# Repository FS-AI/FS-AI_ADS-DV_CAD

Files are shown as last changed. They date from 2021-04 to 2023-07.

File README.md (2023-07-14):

# FS-AI_ADS-DV_CAD

## Introduction

This repository contains CAD data for the IMechE FS-AI ADS-DV for release to participating teams.

The CAD provided is a subset of the whole vehicle CAD and is intended for sensor and / or compute hardware installation and vehicle dynamics modelling purposes.

In particular teams wishing to fit additional sensors and / or compute hardware to a shared IMechE ADS-DV must use this CAD data to gain approval for their installation design. (See section 'Additional Sensor and Compute Mounting CAD Submission and Approval' below).

This CAD data remains Copyright IMechE 2020 and must not be uploaded to alternate public access web / cloud locations. This is both to protect copyright and to ensure there is one 'official' source for CAD data that may be up-issued by the IMechE as necessary. Local clones are encouraged to make it easy for updates to be pulled from the upstream repository using Git.

The URL for this repository is: https://github.com/FS-AI/FS-AI_ADS-DV_CAD

If you are not accessing this repository directly from this URL then likely you are working from a fork or clone which may not contain the latest data or information. If you have made a local clone, please ensure you do a 'git pull' to ensure you have the latest version of all files.

## Updates

The repository will be updated regularly in response to questions and as new information is confirmed and released. Github allows you to 'Watch' the repository so as to be informed of activity.

#### Update 2023-02-23

Clarified that both additional sensor and compute installations are allowed.

#### Update 2021-06-02

CAD models of the various connector types have been added.

## Questions

Please use the Github 'Issues' feature to ask questions regarding this repository. Please label your issue with the tag 'question'.

Best efforts will be made to answer all questions but please allow a few days for a response.

If a general forum style chat is more appropriate, please use the Github 'Discussions' feature.

## Content

The repository consists of the following files:

- 'Readme.md' - this file containing information about the repository.
- '\images' - folder containing the images for 'Readme.md'.
- 'FS-AI_ADS-DV_CAD.f3d' - see below.
- 'FS-AI_ADS-DV_CAD.step' - see below.
- '12V_Power_Mated' .f3d & .step' (added 2021-06-02)
- 'CAN_DE9_Mated'  .f3d & .step' (added 2021-06-02)
- 'RJ45_Ethernet'  .f3d & .step' (added 2021-06-02)
- 'USB_Mated'  .f3d & .step' (added 2021-06-02)

### Fusion 360 File 'FS-AI_ADS-DV_CAD.f3d'

This file is provided in native Fusion 360 format, which means it preserves sketch details, section analysis details and other useful data such as construction geometry.

Fusion 360 is available free-of-charge for non-commercial or educational use. Full details at: https://www.autodesk.co.uk/products/fusion-360/personal

See also this video for information on how to correctly activate the Personal edition of Fusion 360 instead of the 30 day free trial: https://www.youtube.com/watch?v=qJABXBvuoB4&ab_channel=DesktopMakes

### STEP File 'FS-AI_ADS-DV_CAD.step'

This file is a STEP format export of the Fusion 360 file. STEP is a universal file format for import into other CAD packages.

One disadvantage of the STEP format is that it does not preserve the sketch details of the Front and Side view relating to the Surface Envelope definition and the ZED camera sight line. You will need to replicate this sketch geometry within your own CAD package. See the images below.

This STEP file has been tested with FreeCAD v0.19, available here: https://www.freecadweb.org/

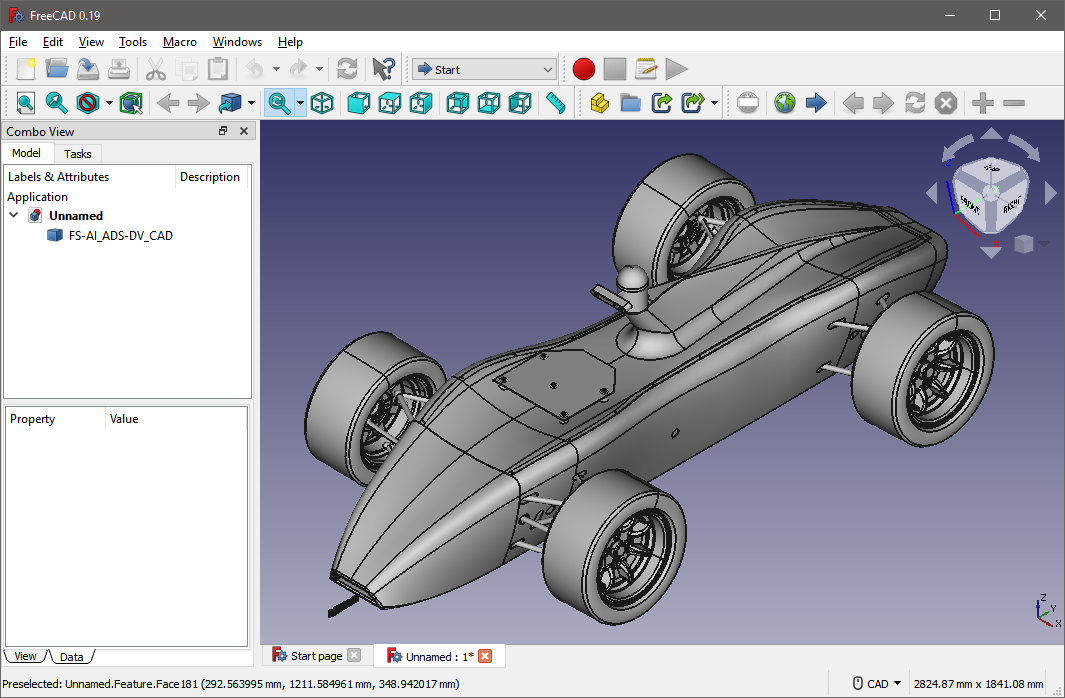
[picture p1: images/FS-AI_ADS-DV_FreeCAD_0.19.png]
FS-AI_ADS-DV_FreeCAD_0.19


## Sketch Views

### Side View

In the case of using the STEP file, see below for the details of the sight line of the ZED camera and the FS-AI Rule T 1.3.3 Surface Envelope in side view.

The ZED camera reference angle is 15deg below horizontal. A normal line projected from the centre of the front face of the ZED camera will intersect the ground plane approximately 2750mm from the camera position.

FS-AI Rule T 1.3.3 defines a 'Surface Envelope' in side view from the top of the ADS-DV TSAL to the outer profile of the tyres. Rule T 1.3.3 further requires that all sensors and / or compute hardware be located within this surface envelope. Since the ADS-DV does not have a traditional roll hoop, the envelope is defined from the outer profile of the TSAL dome. The tyre profile is projected as a 515mm diameter circle on the vehicle centreline.

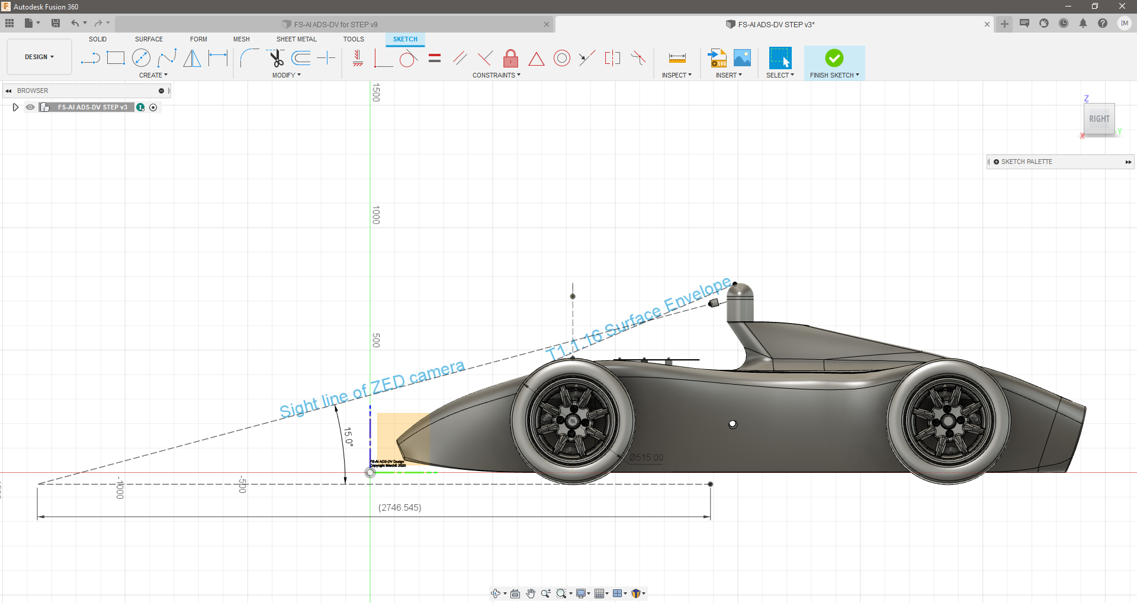
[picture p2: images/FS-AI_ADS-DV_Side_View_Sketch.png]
FS-AI ADS-DV Side View Sketch


### Front View

In the case of using the STEP file, see below for the details of the Rule T 1.3.3 Surface Envelope in front view.

FS-AI Rule T 1.3.3 defines a 'Surface Envelope' in front view from the top of the ADS-DV TSAL to the outer profile of the tyres. Rule T 1.3.3 further requires that all sensors and / or compute hardware be located within this surface envelope. Since the ADS-DV does not have a traditional roll hoop, the envelope is defined from the outer profile of the TSAL dome instead. The tallest point on the tyre profile is used.

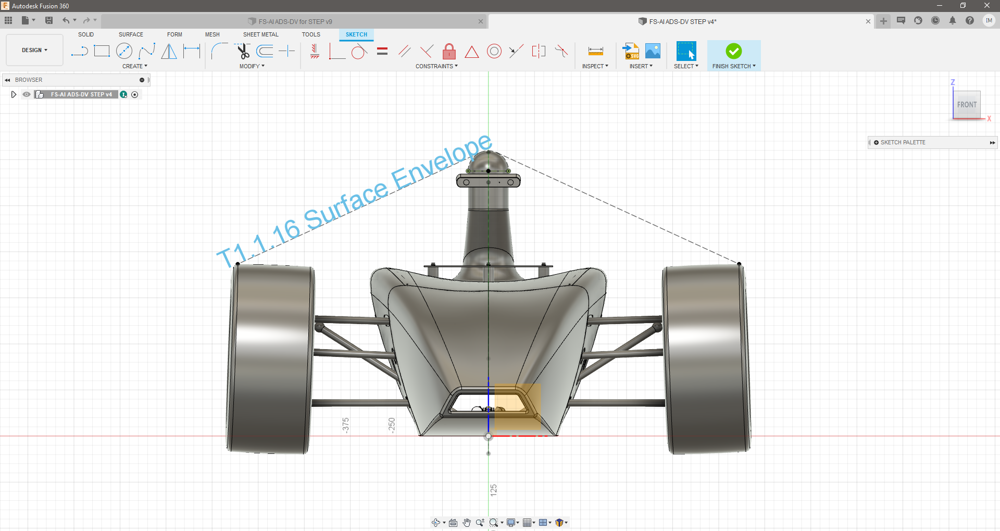
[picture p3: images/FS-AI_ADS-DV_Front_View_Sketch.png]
FS-AI ADS-DV Front View Sketch


### Section View

In the case of using the STEP file the Analysis - Section2 view is not available and is reproduced in the screenshot below.

The nominal reference design for an Additional Sensor and Compute Mounting is a plate spaced 100mm up from the internal chassis using 26mm (or 1.0") diameter spacer pillars. A 120mm M6 bolt is required to ensure sufficient thread engagement into the M6 nut plates of the chassis. A metal spring lock washer and plain metal backing washer are required to ensure the integrity of the mounting.

The full Additional Sensor and Compute Mounting requirements are discussed below.

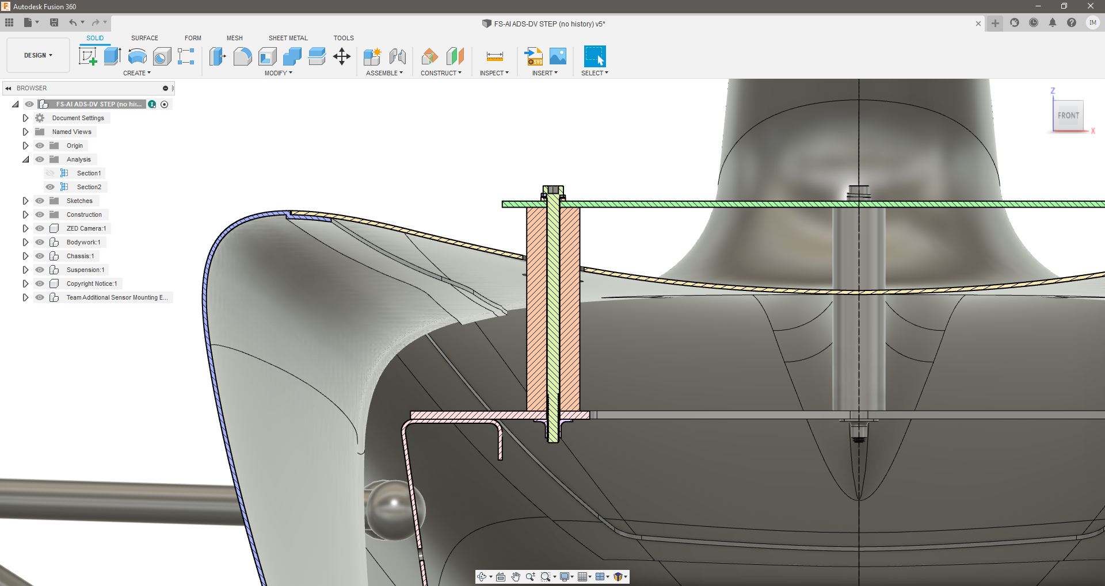
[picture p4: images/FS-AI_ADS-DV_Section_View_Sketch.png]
FS-AI ADS-DV Section View Sketch


## Additional Sensor and Compute Mounting

Teams wishing to mount additional sensors and / or compute hardware to the ADS-DV must adhere to the following requirements:

### Surface Envelope (FS-AI Rules T 1.3.3)

Additional Sensors, Compute hardware and all mounting hardware **must** fit within both the Side View and Front View Surface Envelopes defined above.

**NOTE:** FS-AI Rule T 1.3.4 prohibits teams using a **shared** IMechE ADS-DV from using the 700mm x 500mm forward sensor zone.

### Mounting Requirements

The nominal reference design for an Additional Sensor and Compute Mounting is a plate spaced 100mm up from the internal chassis using 26mm (or 1.0") diameter spacer pillars. This is provided as an example in the CAD data. The example uses all 5 available mounting locations.

Alternate designs are permissible and will be evaluated as part of the approval process.

To safely and securely mount additional sensors the following requirements must be respected:

- **At least 3** mounting pillar locations **must be used**, out of the 5 available.
- The **only permissible mounting option** is a full-length M6 bolt clamping the mounting structure down onto the vehicle chassis plate. Concepts with more than one thread risk the 'wrong' thread releasing when the additional sensors are removed.
- All clamping surfaces must be parallel to the vehicle chassis plate.
- Metal spring lock washers must be used, backed up with metal plain washers, to ensure sufficient clamping force and integrity of mounting.
- All components must be rigid enough to allow the metal spring lock washers to compress completely when the M6 bolts are tightened.
- 12mm of M6 thread engagement is required below the top face of the vehicle chassis plate.
- Unimpeded vertical access to the M6 bolt heads must be available to allow access for a socket (16mm OD) or hex driver.

#### Note on AV mounts:

Grommet type AV mounts may be used to isolate an additional sensor and compute hardware mounting plate as long as the rigid clamping requirement is respected. It must be possible to fully compress the M6 metal spring washer. This is best achieved using 'top hat' spacers or a rigid spacer tube:

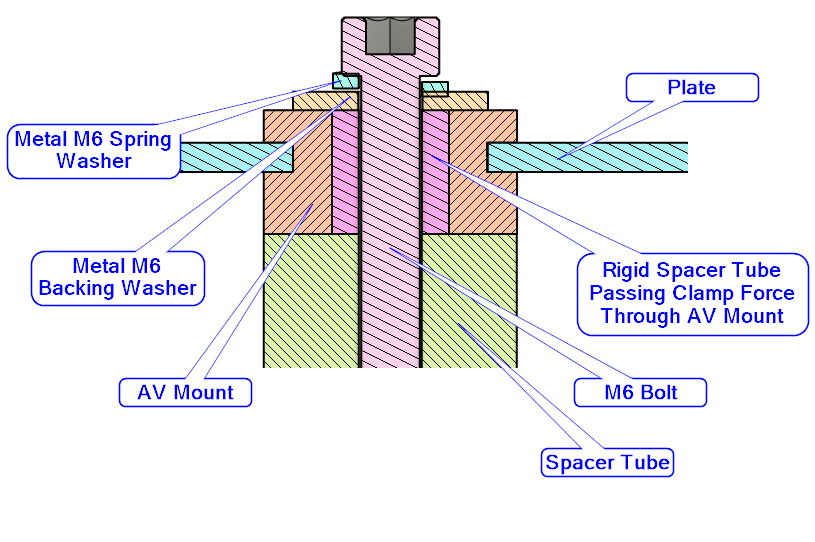
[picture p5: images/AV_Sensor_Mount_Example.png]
AV_Sensor_Mount_Example


### Mounting Locations

The pattern of the position of the mounting locations is as follows:

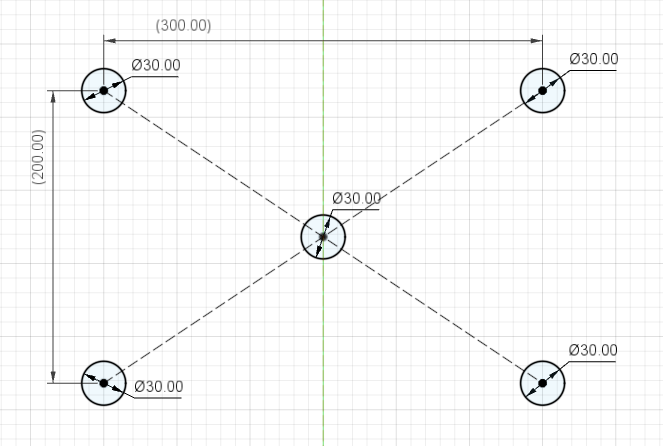
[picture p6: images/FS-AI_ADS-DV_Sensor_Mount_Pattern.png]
FS-AI_ADS-DV_Sensor_Mount_Pattern


The mounting holes are M6 threaded, and the 30mm diameter represents the clearance holes in the bodywork.

#### ToDo:

Example 3D printed mounting plate, showing parallel clamping surfaces, metal spring lock washers and metal plain backing washers.

## Additional Sensor Electrical Connections

The electrical connector location for additional sensors is somewhat flexible and will be confirmed once all teams have submitted an initial design for approval. The preferred location is in the region circled on the image below:

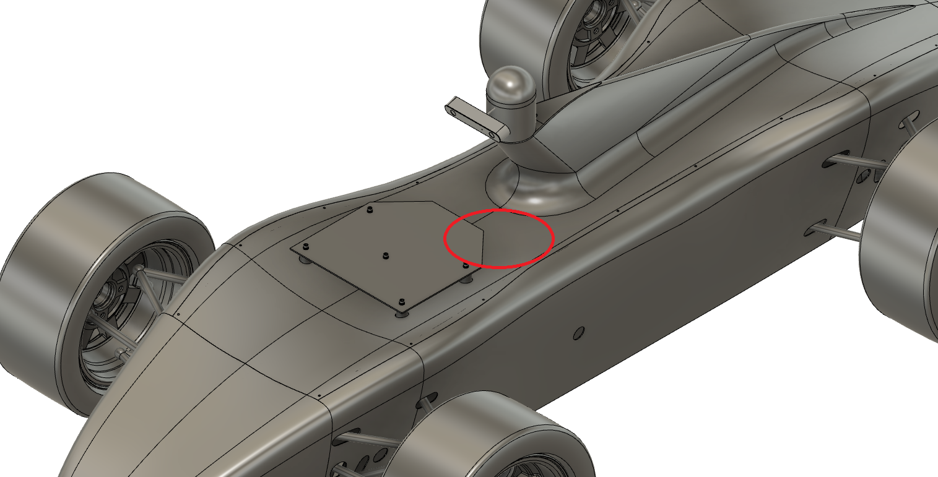
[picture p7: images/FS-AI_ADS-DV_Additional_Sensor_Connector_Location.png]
FS-AI_ADS-DV_Additional_Sensor_Connector_Location


The wiring harness on the vehicle side will allow for a range of movement within this approximate zone. Connecting and disconnecting will be done by moving the vehicle side wiring harness. However additional sensor and compute hardware mounting designs **must allow for strain relief of both sides of the connected wiring**. The strain relief on the vehicle side of the connector(s) should be adjustable for cable diameter and easily removeable. A screwed down cable tie base is the recommended option:

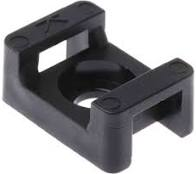
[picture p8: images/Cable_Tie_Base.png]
Cable_Tie_Base


### Vehicle Side Connectors

The vehicle side connectors are described below. All images are **vehicle side connector** you need to supply and fit the **opposite mating connector** to your additional sensor installation.

#### Power

- 1x TE DT06-2S power connector supplying automotive ‘12V’ (11.5 ->14.5V depending on battery charge state) up to 5A. Pin 1 = 12V and Pin 2 = Gnd:

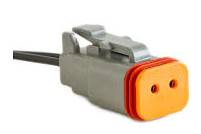
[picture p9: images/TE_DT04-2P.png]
TE_DT04-2P


Mating part number TE DT04-2P.

#### Ethernet

- 2x Ethernet Cat6 cables with the standard RJ45 connector running from 2 Ethernet sockets on the InCarPC:

Ethernet_RJ45

#### USB3.0

- 2x USB3.0 Type A sockets connected via a powered USB3.0 hub to the InCarPC:

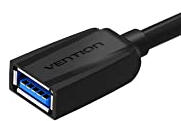
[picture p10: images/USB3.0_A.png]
USB3.0_A


#### CAN

- 1x DE9 connector for CAN on the vehicle. It will be receptacle type, pin contacts and internal thread:

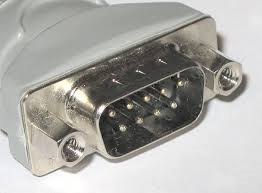
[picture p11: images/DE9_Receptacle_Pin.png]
DE9_Receptacle_Pin


*<u>CAD models of the above connectors have been added on 2021-06-02.</u>*

## Additional Sensor and Compute Mounting CAD Submission for Approval

Teams wishing to fit additional sensors and / or compute hardware to a shared IMechE ADS_DV **must submit CAD data** of their proposed design for approval. Teams should have requested additional sensors and / or compute hardware on their 'DCS' form with full details provided for review in their 'ASF' document. Team leaders should already have been contacted by email with details of this process and contact details for submission. A 'zip' archive should be used to contain all data, labelled with team identification and a version number.

The CAD data should place the sensor and / or compute hardware mounting design in the correct position **within the CAD data provided in this repository** and include the following components / information:

- All additional sensor and compute hardware (space-claim / box models are fine, internal detail is not required).
- Sensor mounting structural components **including spacer tubes.**
- M6 fasteners including all washers.
- All fasteners used to mount sensor and compute hardware, or a description of the mounting technique used (e.g. 3M Dual Lock).
- Information on component materials and manufacturing process.
- Information and / or models regarding the proposed wiring scheme, connector location(s) and the **cable strain relief implementation**.

NOTE: it is the responsibility of the team to provide **all additional sensor mounting components**, nothing is provided with the vehicle except the M6 threaded holes in the vehicle chassis plate.

CAD data file format should be either native Fusion 360 ('.f3d') or STEP ('.stp' / '.step').

Supplementary information should be provided as either a PDF or Markdown file.

----
Don't forget to check the IMechE website regularly for documentation updates:

https://www.imeche.org/events/formula-student/team-information/forms-and-documents

## For specific questions and bug reports, please raise an Issue and tag it with the 'question' label.
#### Otherwise, please use the Github Discussions feature for general forum-style chat.

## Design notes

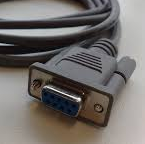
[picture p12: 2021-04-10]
images/DE9_Plug_Socket.png

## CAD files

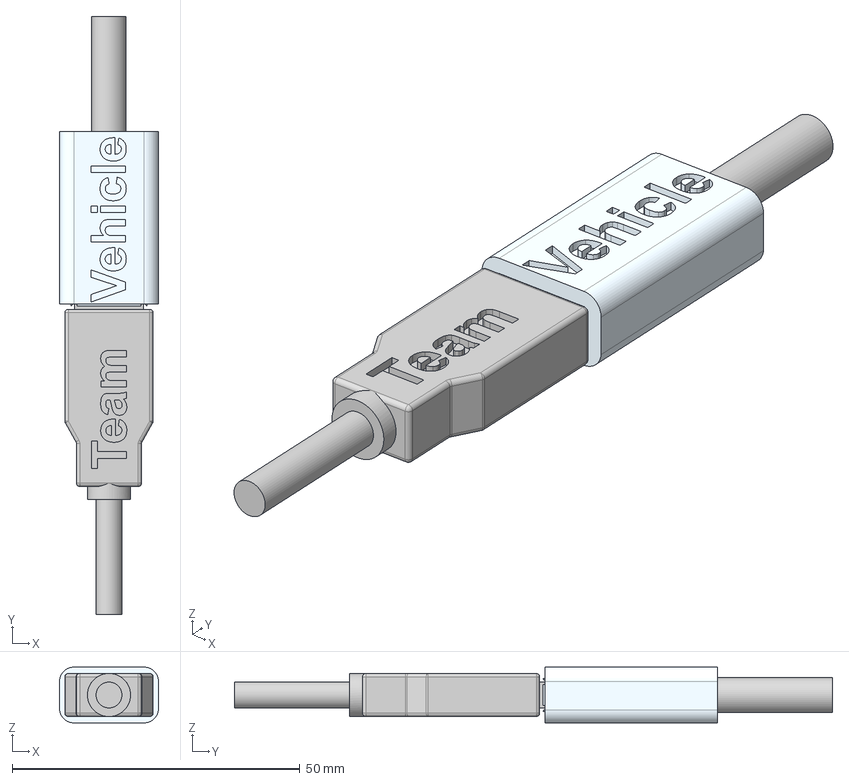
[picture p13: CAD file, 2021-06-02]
USB_Mated.step
17.2 x 103.9 x 9.70 mm
USB_A_Plug v2
USB_A_Socket v2

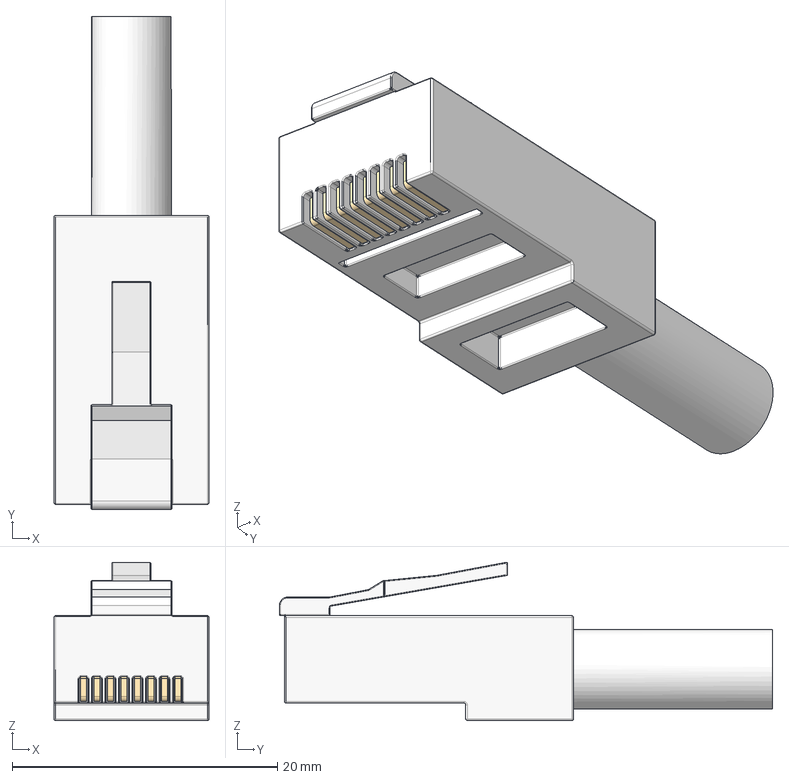
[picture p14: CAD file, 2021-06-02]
RJ45_Ethernet.step
11.7 x 37.2 x 11.9 mm

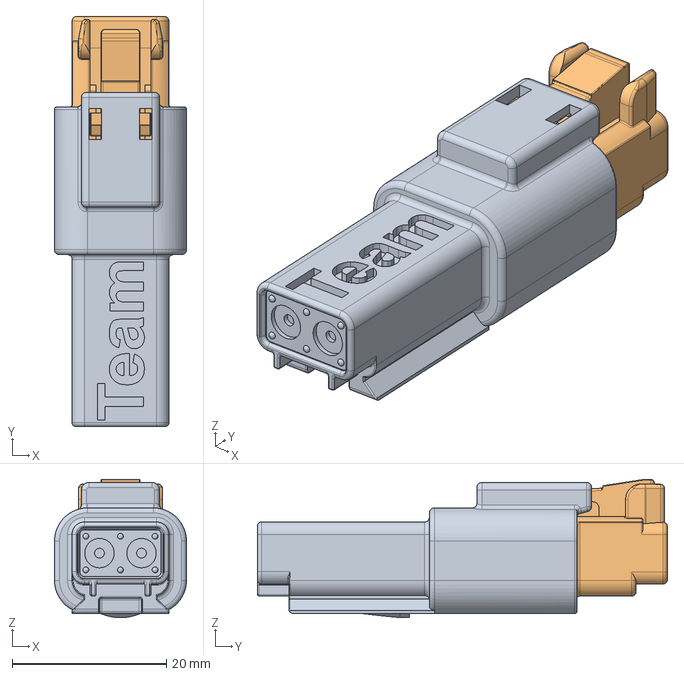
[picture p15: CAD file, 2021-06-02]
12V_Power_Mated.step
17.1 x 53.2 x 18.0 mm
DT04-2P v1
DT06-2S v1

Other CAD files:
12V_Power_Mated.f3d
CAN_DE9_Mated.f3d
RJ45_Ethernet.f3d
USB_Mated.f3d

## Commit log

2021-04-10 Initial CAD upload.
2021-06-02 Added connector models.
    [12V_Power_Mated.f3d, 12V_Power_Mated.step, CAN_DE9_Mated.f3d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]
2023-07-14 Update README.md
    Added power connector polarity.
